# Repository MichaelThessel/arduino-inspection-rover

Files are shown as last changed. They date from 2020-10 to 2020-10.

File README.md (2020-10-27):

# Camera inspection rover

This repository contains the firmware and the CAD files used to construct a
basic camera inspection rover.

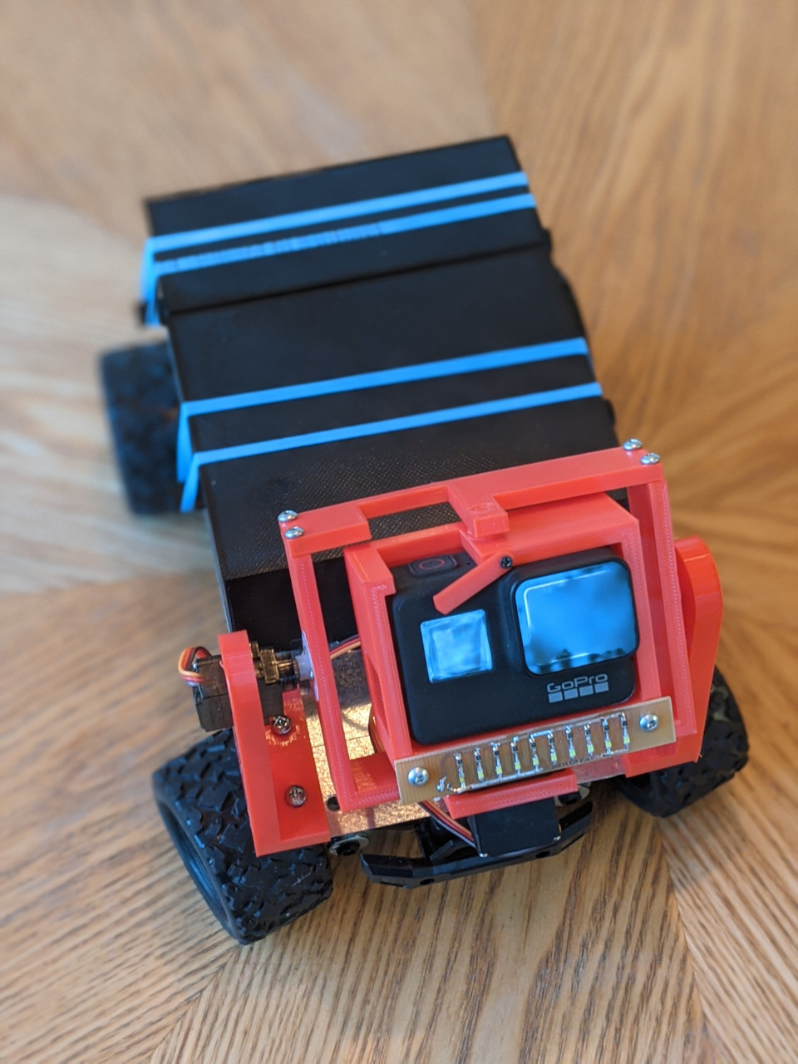
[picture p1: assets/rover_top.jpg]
Rover (top)


# Components

The rover is build based on a modified 1:18 scale RC car.
The model used here is a PulseLabZ HS18321 but this should work with pretty much
any RC car.

The car is modified to work with a Futaba R2004GF 2.4GHz 4 channel receiver.

2 Channels of the receiver control the servos for the X and Y axis of the camera
gimbal. One channel controls the motor speed and the remaining channel controls
the servo for the steering.

The 2 servos in the gimbal are Hobby King HK-933MG.

For the motor speed controller I opted for the Hobbywing Quicrun 1060 60A 2S-3S
ESC (brushed).

# Gimbal

The gimbal is a custom design meant for a GoPro 7. It uses 2 standard RC servos.

The cad files for the gimbal are in the [cad/gimbal](cad/gimbal) directory.

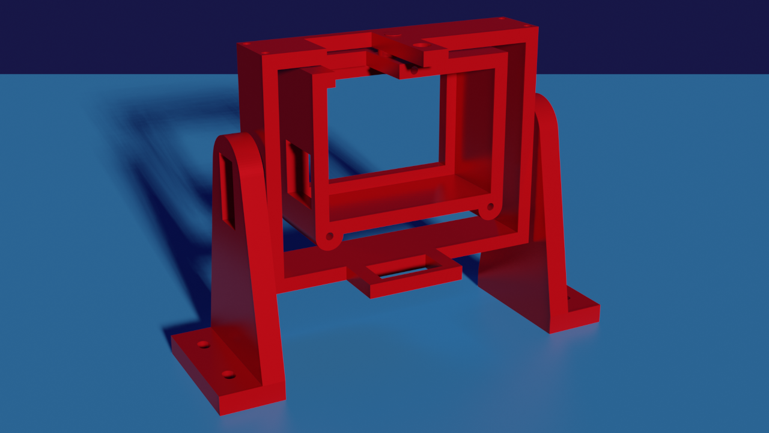
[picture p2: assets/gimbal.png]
Gimbal


The gimbal also has a light bar attached. The light bar is a simple custom
etched PCB with 0805 LEDs (white) and 0805 resistors (220R).

The design files for the light bar are in the [pcb/light-bar](pcb/light-bar)
directory.

The STL files for the gimbal are also available on
[Thingiverse](https://www.thingiverse.com/thing:4635363).

# Motor control

One of the challenges was that the RC car was meant to go fast.  For the
intended use case a slow speed was desired though. Simply being careful with the
control sticks wasn't really working as the slightest input resulted in
significant acceleration.

I used an Arduino Pro Mini to sample the PWM signal from the RC receiver and
then mapped it into a new PWM signal that would drive the motor at a reduced
speed. This also accounts for the fact that the car normally drives faster when
going forward than going backward when given the same input. With the custom
firmware the forward and reverse speed is the same.

The firmware for the motor control is in the [src/firmware](src/firmware)
directory.

# Steering

Another issue was that the servo to control the steering was a 5 wire servo and
not a conventional 3 wire servo. To make the steering servo compatible with the
RC receiver I transplanted the electronics from a standard 3 wire servo into
the 5 wire servo.

The process for that is quite straight forward. There is a good video available
[here](https://www.youtube.com/watch?v=GDukjyycyxo).

# Enclosures

The rover uses 2 enclosures. One for the battery and one for the rest of the
electronics. The reason to separate this is to prevent having to access the
electronics compartment when switching out the battery.

The cad files for the enclosures are in the [cad/box](cad/box) directory.

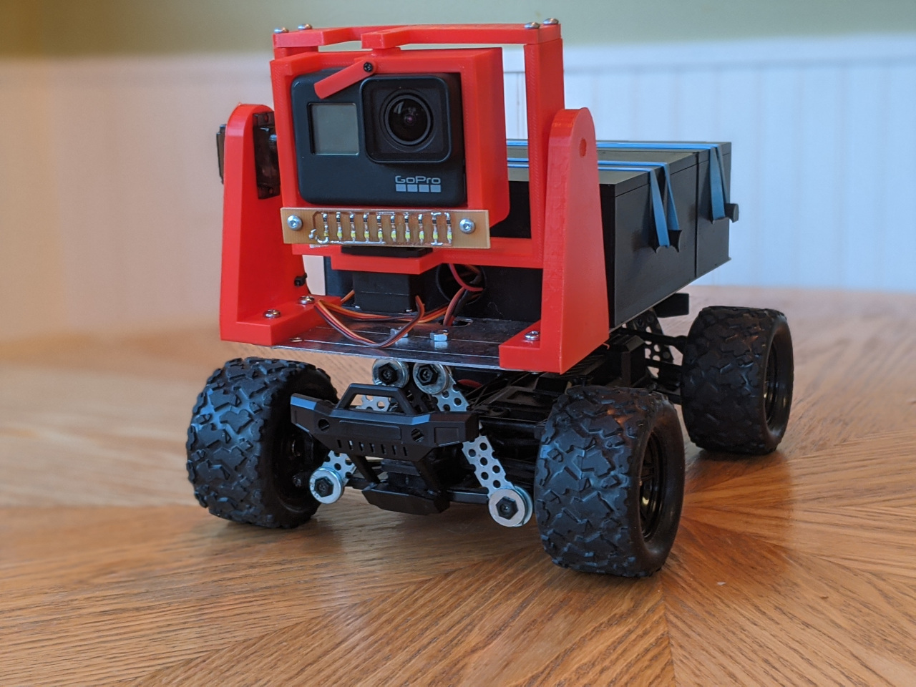
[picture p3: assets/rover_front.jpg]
Rover (front)


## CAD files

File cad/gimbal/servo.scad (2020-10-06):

include <variables.scad>

// Cutout for servo body
module servoCutout(thickness) {
    cube([servoWidth, servoHeight, thickness]);
}

// Cutout for servo mounting plate
module servoPlateCutout() {
    cylinder(h = servoPlateThickness + DIFFERENCE_FIX_2, r = servoPlateRadius);
}

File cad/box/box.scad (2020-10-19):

include <variables.scad>

box();

/*
color([1, 0, 1])
translate([0, boxHeight, boxDepth + lidThickness])
rotate([180, 0, 0])
*/
*lid();

module box() {
    difference() {
        boxWithMounts();

        if (boxType == "battery") {
            translate([boxWidth / 2, 0, powerSwitchHoleOffsetZ])
            powerSwitchHole();
        } else {
            // Cable hole front
            translate([boxWidth / 2, 0, cableHoleOffsetZ])
            cableHole();
        }

        // Cable hole front
        translate([boxWidth / 2, boxHeight - boxThickness, cableHoleOffsetZ])
        cableHole();
    }

    translate([0, boxHeight / 2, boxDepth / 2])
    rubberBandHolder();

    translate([boxWidth + rubberBandHolderHeight, boxHeight / 2, boxDepth / 2])
    rubberBandHolder();
}

// Box with mounting holes
module boxWithMounts() {
    difference() {
        union() {
            boxBody();

            translate([holeOffsetX, holeOffsetY, 0])
            holeBody();

            translate([boxWidth - holeOffsetX, holeOffsetY, 0])
            holeBody();

            translate([holeOffsetX, boxHeight - holeOffsetY, 0])
            holeBody();

            translate([boxWidth - holeOffsetX, boxHeight - holeOffsetY, 0])
            holeBody();
        }

        translate([holeOffsetX, holeOffsetY, 0])
        holeHole();

        translate([boxWidth - holeOffsetX, holeOffsetY, 0])
        holeHole();

        translate([holeOffsetX, boxHeight - holeOffsetY, 0])
        holeHole();

        translate([boxWidth - holeOffsetX, boxHeight - holeOffsetY, 0])
        holeHole();
    }
}

// Box body
module boxBody() {
    difference() {
        cube([boxWidth, boxHeight, boxDepth]);

        translate([boxThickness, boxThickness, boxThickness + DIFFERENCE_FIX])
        cube([boxWidth - boxThickness * 2, boxHeight - boxThickness * 2, boxDepth - boxThickness + DIFFERENCE_FIX]);
    }

}

// Mounting hole
module hole() {
    difference() {
        holeBody();
        holeHole();
    }
}

// Mounting hole body
module holeBody() {
    translate([-holeRadius / 2, 0 , 0])
    hull() {
        cylinder(r = holeRadius + holeWallThickness, h = boxThickness * 2 + 0);
        translate([holeRadius, 0, 0])
        cylinder(r = holeRadius + holeWallThickness, h = boxThickness * 2 + 0);
    }
}

// Mounting hole hole
module holeHole() {
    translate([-holeRadius / 2, 0 , 0])
    hull() {
        cylinder(r = holeRadius, h = boxThickness * 2 + 0);
        translate([holeRadius, 0, 0])
        cylinder(r = holeRadius, h = boxThickness * 2 + 0 + 0);
    }
}

// Lid for box
module lid() {
    cube([boxWidth, boxHeight, lidThickness]);
    translate([boxThickness + lidPlateOffset, boxThickness + lidPlateOffset, lidThickness])
    cube([
        boxWidth - boxThickness * 2 - lidPlateOffset * 2,
        boxHeight - boxThickness * 2 - lidPlateOffset * 2,
        lidPlateThickness
    ]);

}

// Rubber band holder
module rubberBandHolder() {
    rotate([0, 270, 0])

    difference() {
        cylinder(r = rubberBandHolderRadius, h = rubberBandHolderHeight);

        translate([-rubberBandHolderRadius, rubberBandHolderHeight / 2, rubberBandHolderHeight / 2])
        rotate([90, 0, 0])
        cylinder(r = rubberBandHolderRadius, h = rubberBandHolderHeight);
    }
}

// Hole for power switch
module powerSwitchHole() {
    rotate([270, 0, 0])
    cylinder(r = powerSwitchHoleRadius, boxThickness);
}

// Hole for cables
module cableHole() {
    rotate([270, 0, 0])
    cylinder(r = cableHoleRadius, boxThickness);
}

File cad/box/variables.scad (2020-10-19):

$fn = 100;

// General
DIFFERENCE_FIX = 0.1;
DIFFERENCE_FIX_NEGATIVE = -1 * DIFFERENCE_FIX;
DIFFERENCE_FIX_2 = 2 * DIFFERENCE_FIX;

boxType = "battery";
//boxType = "electronics";

boxWidth = 128;
boxHeight = boxType == "battery" ?  50 : 100;
boxDepth = 50;

boxThickness = 5;

holeRadius = 2;
holeWallThickness = 3;
holeOffsetX = 10;
holeOffsetY = 10;

rubberBandHolderRadius = 5;
rubberBandHolderHeight = 10;

lidThickness = boxThickness;
lidPlateOffset = 0.2;
lidPlateThickness = 2;

powerSwitchHoleRadius = 3;
powerSwitchHoleOffsetZ  = 12;

cableHoleRadius = 10;
cableHoleOffsetZ = 15;

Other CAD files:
cad/gimbal/camera_mount.scad
cad/gimbal/frame.scad
cad/gimbal/frame_bottom.scad
cad/gimbal/frame_top.scad
cad/gimbal/gimbal.scad
cad/gimbal/lock.scad
cad/gimbal/support.scad
cad/gimbal/support_left.scad
cad/gimbal/support_right.scad
cad/gimbal/variables.scad

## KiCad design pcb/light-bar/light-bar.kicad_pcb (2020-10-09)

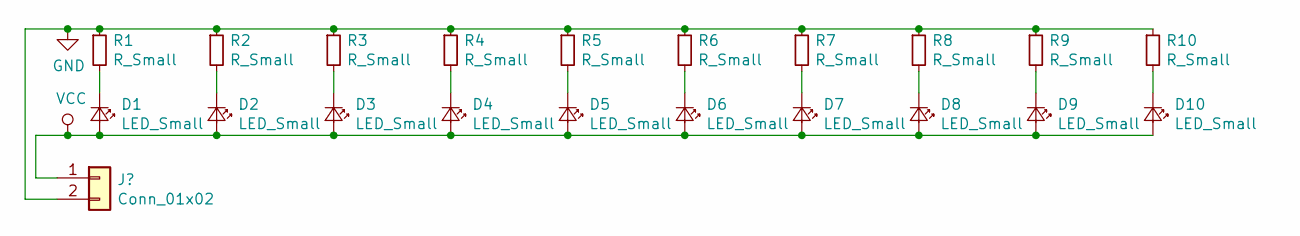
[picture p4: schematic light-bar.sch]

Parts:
D1, D2, D3, D4, D5, D6, D7, D8, D9, D10: LED_Small; LED_0805_2012Metric
R1, R2, R3, R4, R5, R6, R7, R8, R9, R10: R_Small; R_0805_2012Metric

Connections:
GND: R1.1, R2.1, R3.1, R4.1, R5.1, R6.1, R7.1, R8.1, R9.1, R10.1; also elsewhere on the board
unnamed: D1.1 (K), R1.2
unnamed: D2.1 (K), R2.2
unnamed: D3.1 (K), R3.2
unnamed: D4.1 (K), R4.2
unnamed: D5.1 (K), R5.2
unnamed: D6.1 (K), R6.2
unnamed: D7.1 (K), R7.2
unnamed: D8.1 (K), R8.2
unnamed: D9.1 (K), R9.2
unnamed: D10.1 (K), R10.2
VCC: D1.2 (A), D2.2 (A), D3.2 (A), D4.2 (A), D5.2 (A), D6.2 (A), D7.2 (A), D8.2 (A), D9.2 (A), D10.2 (A); also elsewhere on the board

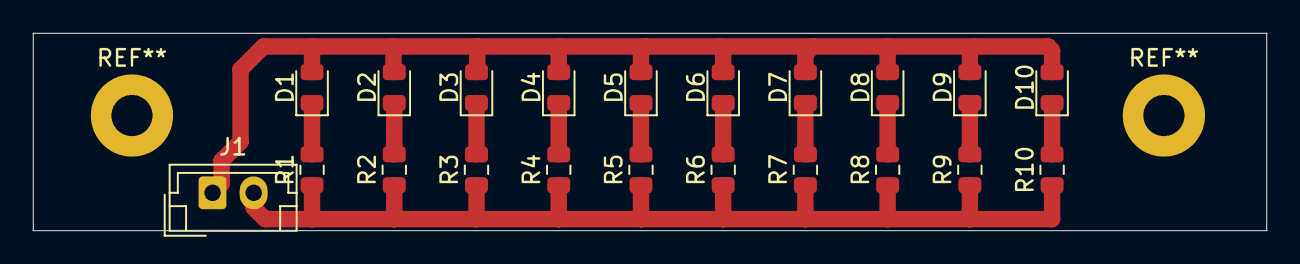
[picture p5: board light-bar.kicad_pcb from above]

Board: 2 copper layers, 75.0 x 12.0 mm, 21 parts (0 on the bottom side), 12 nets.

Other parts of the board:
J1: Conn_01x02; JST_EH_B2B-EH-A_1x02_P2.50mm_Vertical

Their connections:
GND: J1.2; also elsewhere on the board
VCC: J1.1; also elsewhere on the board

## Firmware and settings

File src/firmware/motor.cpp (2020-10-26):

#include "Arduino.h"
#include "debug.h"
#include "motor.h"
#include "pwmsample.h"

extern uint8_t PWM_PIN_INPUT_Y;
extern uint8_t PWM_PIN_OUTPUT_Y;

PWMSample* ISRinputY;

/**
 * Control motor speed
 */
Motor::Motor() {}

/**
 * Set up Motor
 */
void Motor::setup() {
    this->inputY = new PWMSample(PWM_PIN_INPUT_Y, this->PWM_CENTER);

    // Make PWM sampler available to ISR(PCINTx_vect)
    ISRinputY = this->inputY;

    // Enable PIN change interrupts for pins for output PWM
    PCMSK0 |= _BV(PCINT4);

    // Enable PIN change interrupts
    PCICR = _BV(PCIE2) | _BV(PCIE0);

    this->outputY = new PWMGenerate(PWM_PIN_OUTPUT_Y);
    this->outputY->initTimer();
}

/**
 * Reads current receiver Y PWM pulse width and converts it in to motor movements
 */
void Motor::readInput() {
    // Debounce input
    if (millis() < this->lastRead + this->DEBOUNCE_DELAY) {
        return;
    }
    this->lastRead = millis();

    float py = this->inputY->getWidth();

    DPRINTF("Detected pulse width: ");
    DPRINT(py);
    DPRINTLNF("");

    // Pulse width range reciever:
    // Center = 1500
    // Top    = 2000
    // Bottom = 1000

    // Position range:
    // Total steps = 544
    // Steps for each direction = 272
    //
    // regular mapping
    // mappingFactor = 500 / 272 = 1.84
    //
    // the motor does run faster forward for the same PWM signal; compensate for
    // that
    float forwardMappingFactor = 2.4;
    float backWardMappingFactor = 1.8;

    int position = 0;
    if (py < PWM_CENTER_BOUNDARY_MAX) {
        position = (int) (1500 - py) / forwardMappingFactor;
    } else if (py > PWM_CENTER_BOUNDARY_MIN) {
        position = (int) (1500 - py) / backWardMappingFactor;
    }

    DPRINTF("Setting position: ");
    DPRINT(position);
    DPRINTLNF("");

    this->outputY->setPosition(position);
}

/**
 * ISR for when change on X axis is detected
 */
ISR(PCINT0_vect) {
    ISRinputY->ISR_PWM_SAMPLE();
}

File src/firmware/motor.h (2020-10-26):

#ifndef motor_h
#define motor_h

#include "Arduino.h"
#include "pwmgenerate.h"
#include "pwmsample.h"

class Motor
{
    public:
        Motor();
        void setup();
        void readInput();

    private:
        const uint16_t PWM_DELTA = 50;
        const uint16_t PWM_CENTER = 1500;
        const uint16_t PWM_CENTER_BOUNDARY_MIN = Motor::PWM_CENTER - Motor::PWM_DELTA;
        const uint16_t PWM_CENTER_BOUNDARY_MAX = Motor::PWM_CENTER + Motor::PWM_DELTA;

        const uint16_t DEBOUNCE_DELAY = 300;
        unsigned long lastRead = 0;

        PWMSample *inputY;
        PWMGenerate *outputY;
};
#endif

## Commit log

2020-09-09 Added camera control
2020-09-14 Added PWM signal generation
2020-09-18 Added gimbal CAD files
    [gimbal.scad, support.scad, variables.scad]
2020-09-19 Added camera mount
    [camera_mount.scad, gimbal.scad, support.scad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]
2020-09-19 Added camera mount back cutout
    [camera_mount.scad, gimbal.scad, variables.scad]
2020-09-20 Added difference fix
    [camera_mount.scad, support_right.scad, variables.scad]
2020-09-20 Positioned gimbal components
    [gimbal.scad]
2020-09-20 Added frame
    [frame.scad, gimbal.scad, variables.scad]
2020-09-21 Reduced support dimensions
    [variables.scad]
2020-09-23 Only use timer 1 to control x and y axis
2020-10-02 Added frame servo cutout and mounting pin
    [frame.scad, gimbal.scad, support_left.scad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]
2020-10-02 Refined camera mount
    [camera_mount.scad, frame.scad, gimbal.scad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]
2020-10-06 Added screw holes
    [gimbal.scad, support.scad]
2020-10-06 Renamed variable
    [support.scad, variables.scad]
2020-10-06 Added cutout for camera shutter to frame
    [frame.scad, gimbal.scad, variables.scad]
2020-10-06 Changed camera mount offset
    [gimbal.scad]
2020-10-06 Improved support design
    [support.scad]
2020-10-06 Added servo cutout
    [frame.scad, gimbal.scad, servo.scad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]
2020-10-06 Set correct frame height
    [gimbal.scad, variables.scad]
2020-10-06 Corrected camera mount position
    [gimbal.scad]
2020-10-06 Added frame printing templates
    [frame.scad, frame_bottom.scad, frame_top.scad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]
2020-10-06 Added mounting points for LED strip
    [camera_mount.scad, gimbal.scad, variables.scad]
2020-10-06 Added screw hole for lock
    [camera_mount.scad, gimbal.scad]
2020-10-06 Added lock for camera
    [lock.scad, variables.scad]
2020-10-09 Added lightbar PCB
    [light-bar.kicad_pcb, light-bar.sch]
2020-10-09 Moved light bar pcb files
    [light-bar.kicad_pcb, light-bar.sch]
2020-10-09 Moved mounting holes
    [light-bar.kicad_pcb, light-bar.sch]
2020-10-14 Added frame extensions to account for GoPro fisheye lens
    [frame.scad, frame_bottom.scad, frame_top.scad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]
2020-10-19 Added designs for battery and electronics compartment
    [box.scad, variables.scad]
2020-10-19 Increased screw hole radius
    [gimbal.scad, variables.scad]
2020-10-24 Removed camera controls
2020-10-24 Added motor speed control
2020-10-24 Reduced PWM generate to one timer
2020-10-26 Use 16-Bit timer for motor control
